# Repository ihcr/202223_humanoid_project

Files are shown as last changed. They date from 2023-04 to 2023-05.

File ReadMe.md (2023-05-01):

# 22-23 Humanoid Project Repository
This repository contains files for a humanoid robot developed in L4 project by group 93. It contains CAD designs of mechanical structure of a robot, electrical circuit design and low-level control software for its actuation system as well as test results of Unitree A1 motor tests.

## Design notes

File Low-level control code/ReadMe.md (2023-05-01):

# Introduction
This library is used for the communication between PC and multiple motor control boards via multiple converters, so that the user can control the motors by PC. This library only includes Linux version, and we offer the usage example of C++. 

# Dependencies
* [CMake](http://www.cmake.org) (version 2.8.3 or higher)
  
# Files
## /lib
Including the library files of Linux. Please modify the CMakeList manually to select the correst `.so` file.
## /include
Including the header files. ActuationSystem header file is the top-level class encapsulating the library developed for interaction with an actuation system of developed humanoid. 4 functions are needed to use it: constructor, read_actual_positions(), send_desired_positions() and update_torque().
## /src
Including the source files of example, changeID tool, code used for motor testing. The example code can control motors to run under desired command for desired time, and then stop. The main control file is motor_control.cpp which allows for testing the developed ActuationSystem class.
## /build
Build directory. The final executable files are also in this directory.

# Usage
## Setup
Go to configuration.yml and make sure that appropriate lines are commented out as per description above a list. The content of the file should reflect connected setup, i.e. number of converters and number of motors per converter.

## Build
```bash
mkdir build
cd build
cmake ..
make
```
## Run test code
```bash
cd build
sudo ./test_motor
```
## Run the main control
```bash
cd build
sudo ./motor_control
```
## Change ID
```bash
cd build
sudo ./changeID
```

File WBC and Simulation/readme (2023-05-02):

How to run demosntrations for the humanoid robot design:

Install all required libraries to run the WBC

After opening a new terminal, enter the command '. install/setup.bash'

If changing code other than yaml, urdf, or demo files, you must run 'colcon build' to implement the changes.

For Demonstration: Picking up a box off a table:
  
  at the bottom of '/src/limbsim/python/limbsim/env.py', uncomment the section labelled as being for the table demonstration and comment the other sets of objects
  
  run 'python3 src/arm_ik_wbc/demos/humanoid_demo_table.py /configs/project_humanoid_robot.yaml'

For Demonstration: Picking up a box off the floor:
  
  at the bottom of '/src/limbsim/python/limbsim/env.py', uncomment the section labelled as being for the floor demonstration and comment the other sets of objects
  
  run 'python3 src/arm_ik_wbc/demos/humanoid_demo_floor.py /configs/project_humanoid_robot.yaml'

------------------------------------------------------------------------------------------------------------------------------

The final URDF and meshes used in the demonstrations are found in /src/arm_ik_wbc/models/project_humanoid_robot
The final .yaml file used in the demonstrations is found in /src/arm_ik_wbc/configs/project_humanoid_robot.yaml

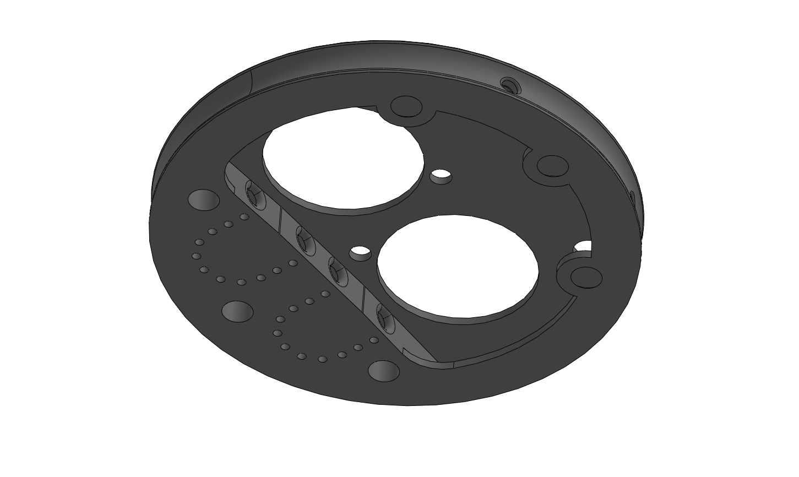
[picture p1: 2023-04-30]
CAD/Arms-Final Design/Images/Pulley-Sheave SLA.png

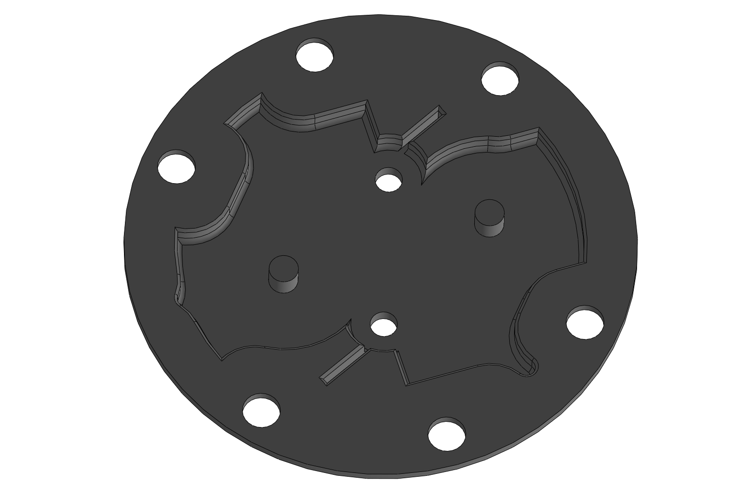
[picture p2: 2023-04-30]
CAD/Arms-Final Design/Images/Pulley-Pretensioner Bracket SLA.png

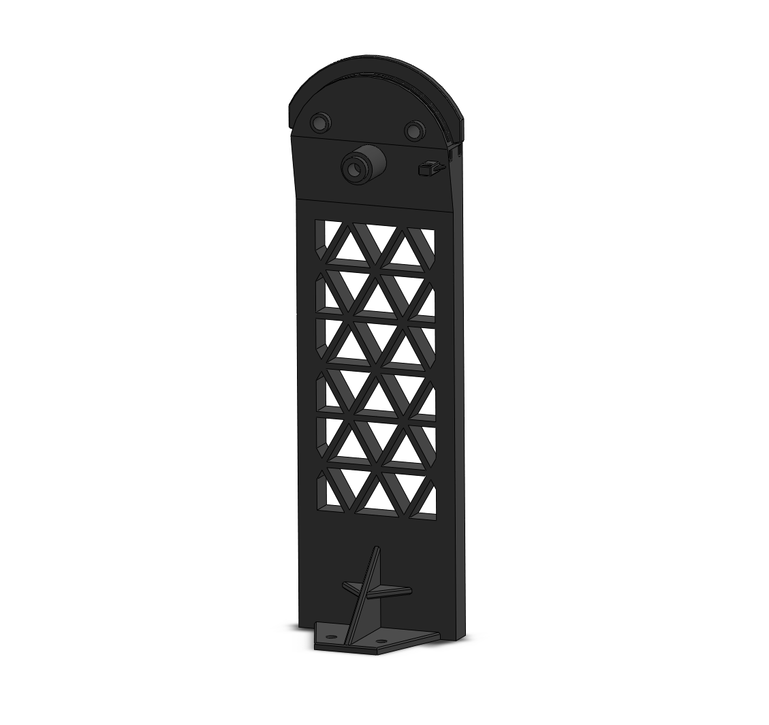
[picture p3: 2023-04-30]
CAD/Arms-Final Design/Images/Skeleton-Forearm Back.png

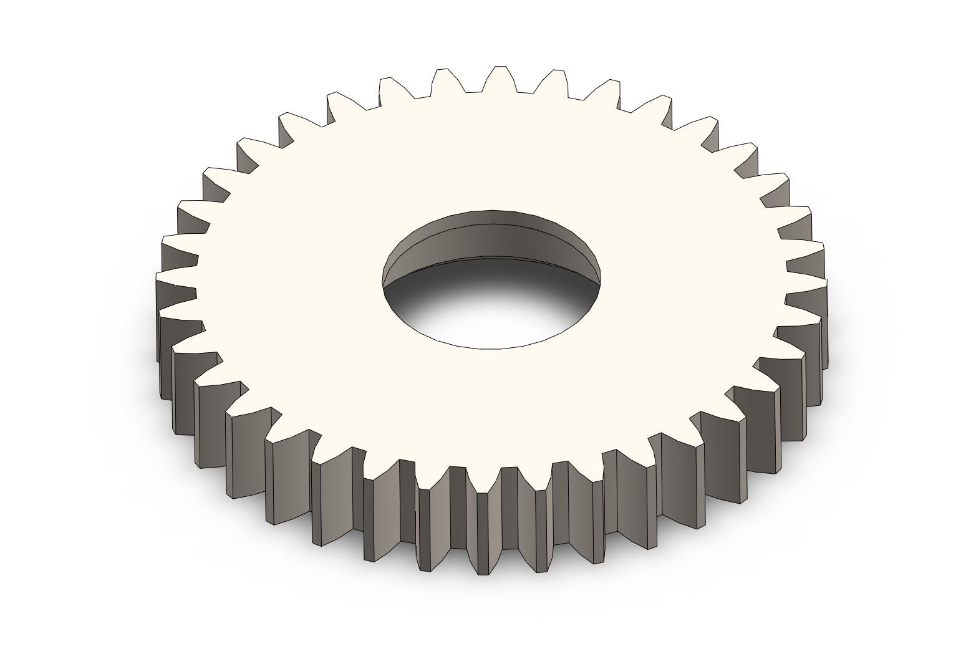
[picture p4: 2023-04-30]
CAD/Arms-Final Design/Images/Planetary Gearbox-Planet.png

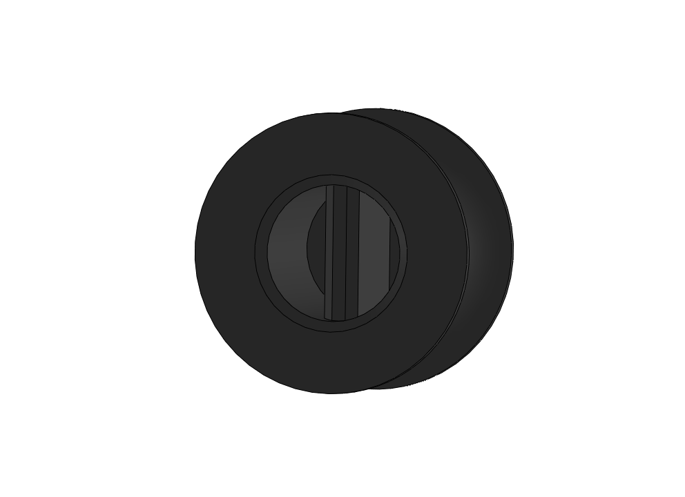
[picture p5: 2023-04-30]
CAD/Arms-Final Design/Images/Pulley-1DOF Fixed.png

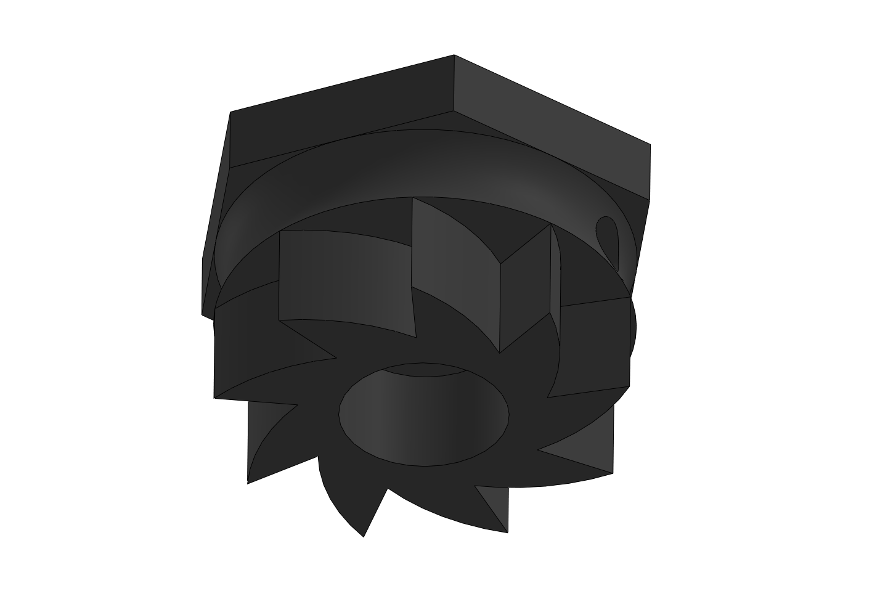
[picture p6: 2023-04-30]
CAD/Arms-Final Design/Images/Pulley-Pretensioner Ratchet SLA.png

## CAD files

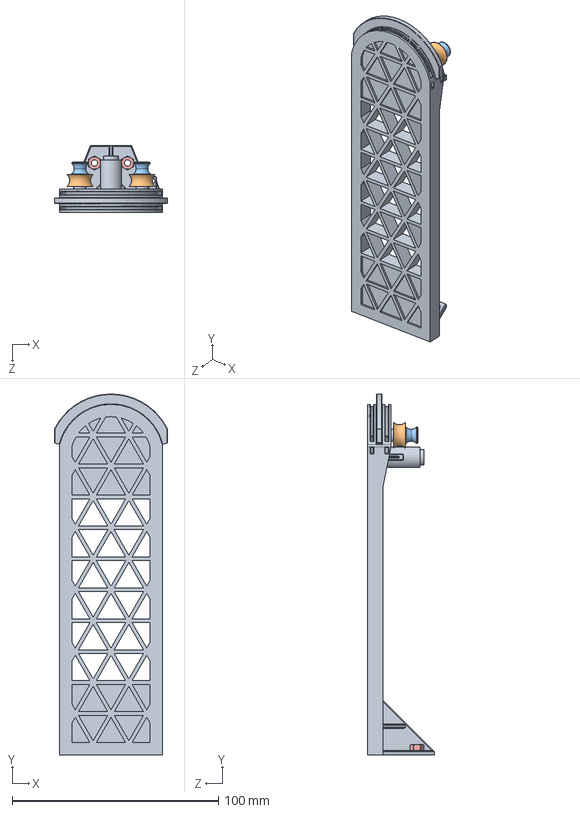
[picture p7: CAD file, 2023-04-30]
CAD/Arms-Final Design/SLDWRKS/Forearm Assembly F.SLDASM
54.8 x 175.0 x 32.5 mm
Skeleton-Forearm Front
Pulley-9mm x 2
Pulley-1DOF Fixed x 2
9mm Bearing x 2
M3 Nut x 2

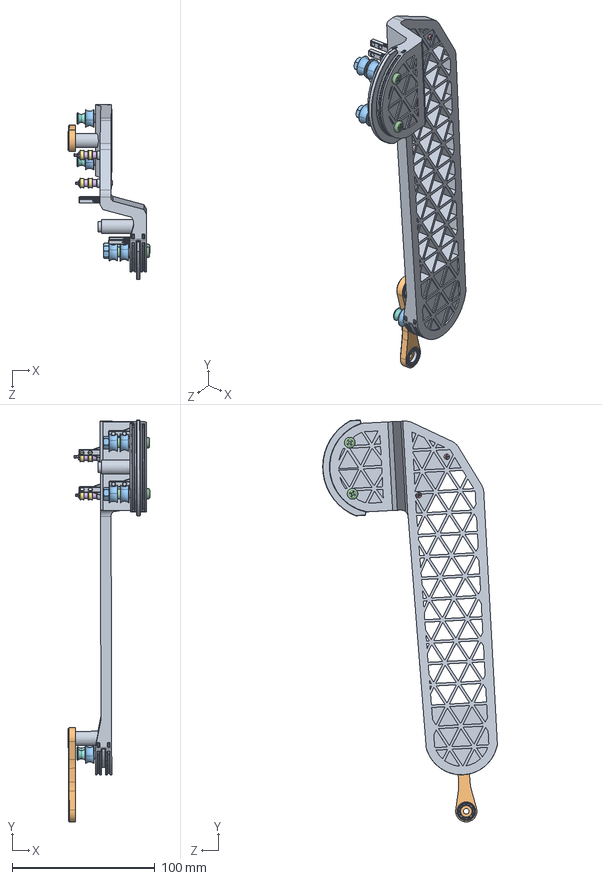
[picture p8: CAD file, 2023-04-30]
CAD/Arms-Final Design/SLDWRKS/Upper Arm Assembly F.SLDASM
57.3 x 282.0 x 122.6 mm
Skeleton-Upper Arm Front
9mm Bearing x 6
Pulley-9mm x 6
Pulley-9mm Spacer x 2
5mm Bearing x 4
Pulley-5mm Spacer x 4
Pulley-5mm ID x 4
Pulley-1DOF Fixed x 2
12mm Bearing x 2
Skeleton-Forearm Connecting Bone
M4 Nut x 2
M4x30 x 2
M2x25 x 2
M2 Nut x 2

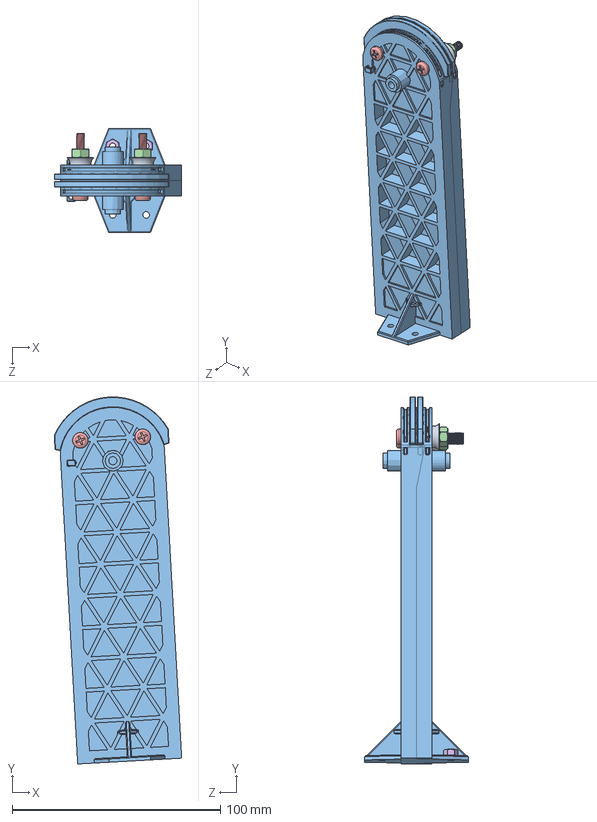
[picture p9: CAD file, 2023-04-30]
CAD/Arms-Final Design/SLDWRKS/Forearm Assembly B.SLDASM
61.2 x 176.1 x 50.0 mm
Pulley-9mm x 2
9mm Bearing x 2
Skeleton-Forearm Back
M4 Nut x 2
M4x30 x 2
M3 Nut x 2

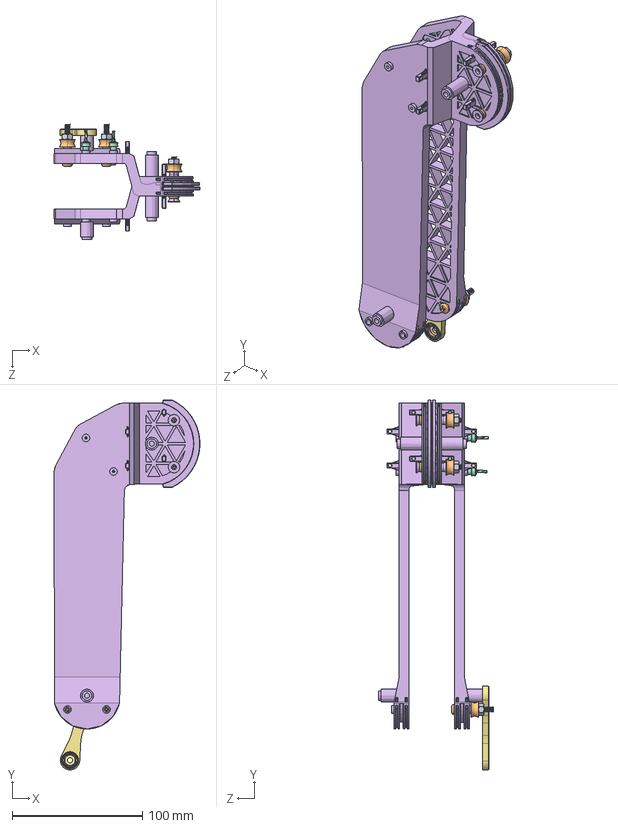
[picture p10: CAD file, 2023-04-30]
CAD/Arms-Final Design/SLDWRKS/Upper Arm Assembly B.SLDASM
111.9 x 283.9 x 88.5 mm
9mm Bearing x 4
Pulley-9mm x 4
5mm Bearing x 2
Pulley-5mm ID x 2
12mm Bearing x 2
Skeleton-Upper Arm Back
Skeleton-Forearm Connecting Bone
Pulley-5mm Spacer x 2
M4 Nut x 4
M4x30 x 4
M2 Nut x 2
M2x25 x 2

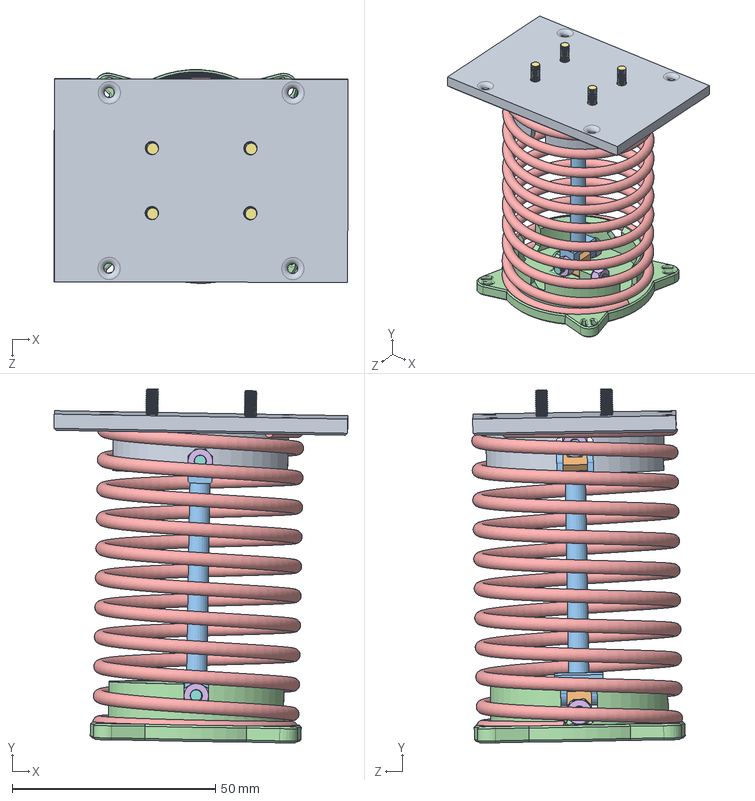
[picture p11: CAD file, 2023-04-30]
CAD/Arms-Final Design/SLDWRKS/Wrist Assembly.SLDASM
72.4 x 87.2 x 52.6 mm
Skeleton-Wrist Top
Skeleton-Wrist Universal Joint Connector x 2
Skeleton-Wrist Linkage
Skeleton-Wrist Bottom
Compression Spring
M3 Nut x 7
M3x10 x 4
M3x20 x 4

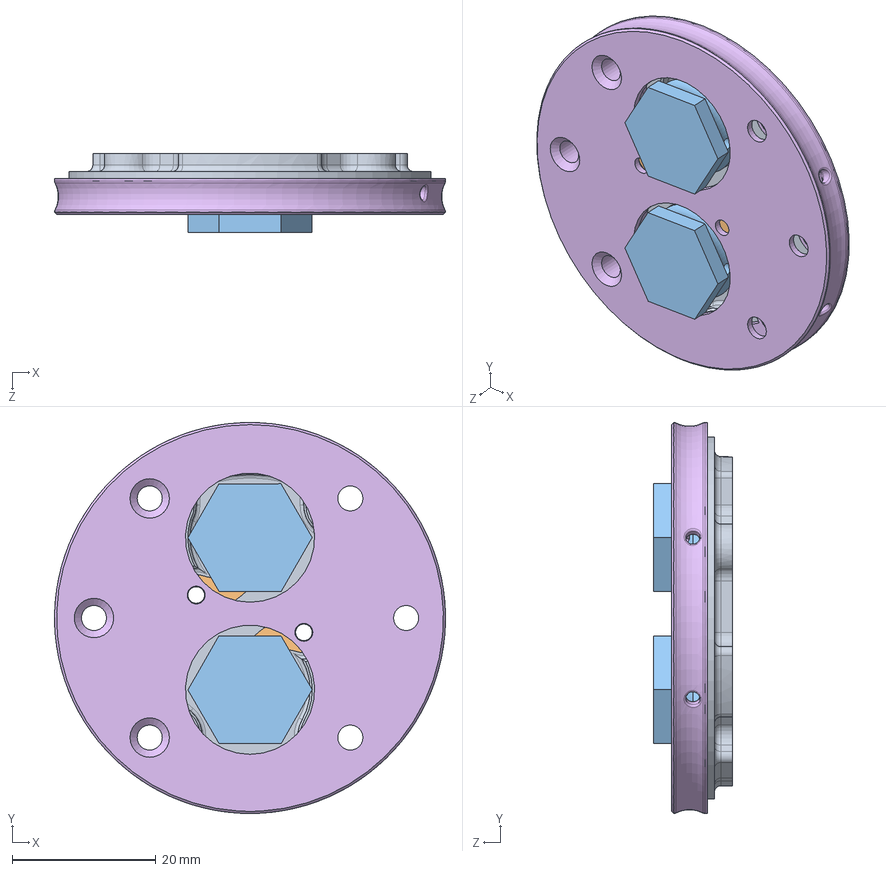
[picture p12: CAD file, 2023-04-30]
CAD/Arms-Final Design/SLDWRKS/Tensioner Assembly SLA.SLDASM
54.5 x 54.5 x 11.0 mm
Pulley-Pretensioner Bracket SLA
Pulley-Pretensioner Pawl SLA x 2
Pulley-Pretensioner Ratchet SLA x 2
6mm Bearing x 2
Torsion Spring x 2
Pulley-Sheave SLA

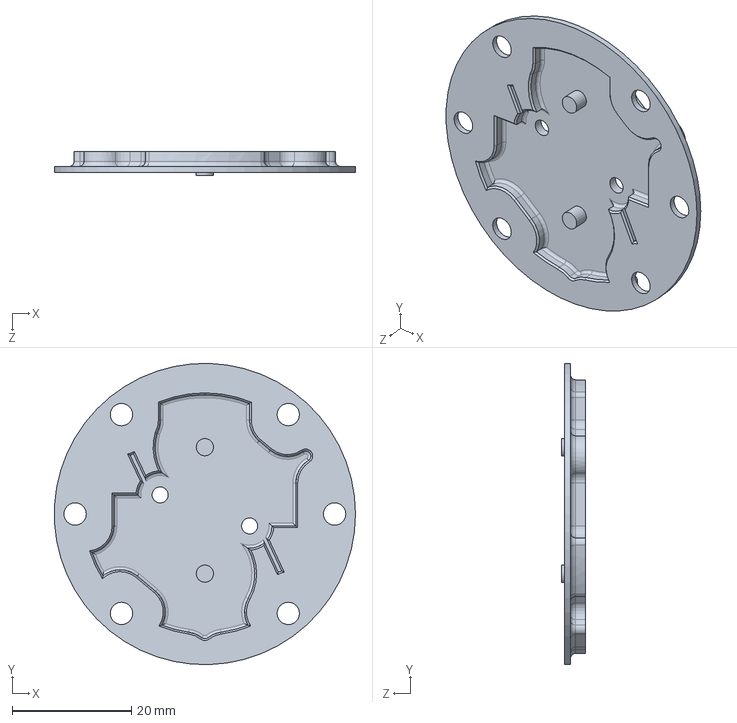
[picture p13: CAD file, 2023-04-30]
CAD/Arms-Final Design/SLDWRKS/Pulley-Pretensioner Bracket SLA.SLDPRT
50.5 x 50.5 x 4.00 mm

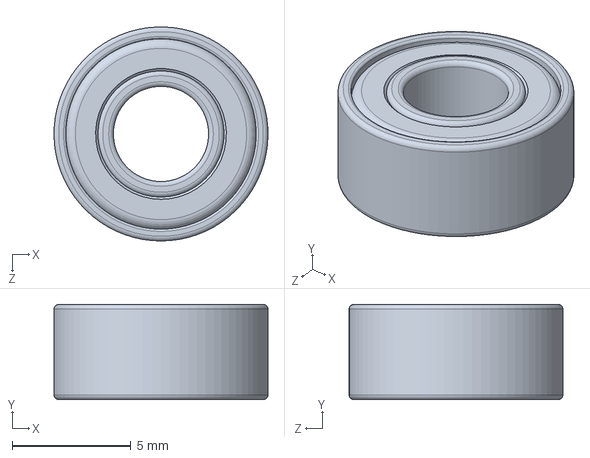
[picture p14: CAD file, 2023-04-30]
CAD/Arms-Final Design/SLDWRKS/Purchased Components/9mm Bearing.SLDPRT
9.00 x 4.00 x 9.00 mm

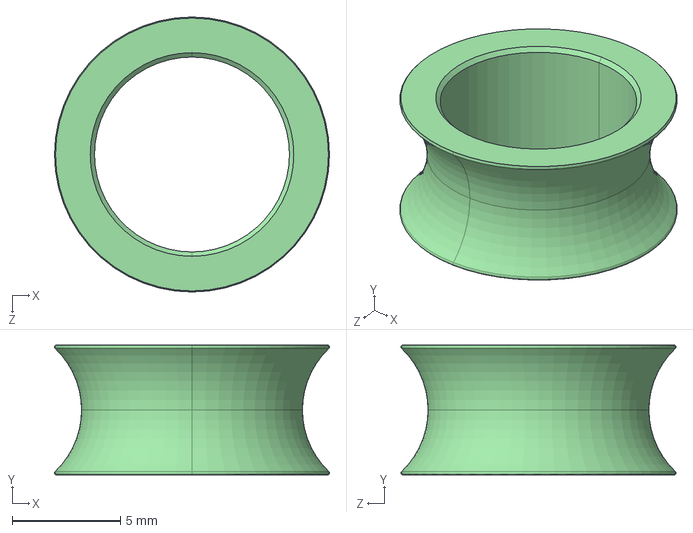
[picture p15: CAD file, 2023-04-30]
CAD/Arms-Final Design/STEP Files/Pulley-9mm.STEP
12.7 x 6.00 x 12.7 mm

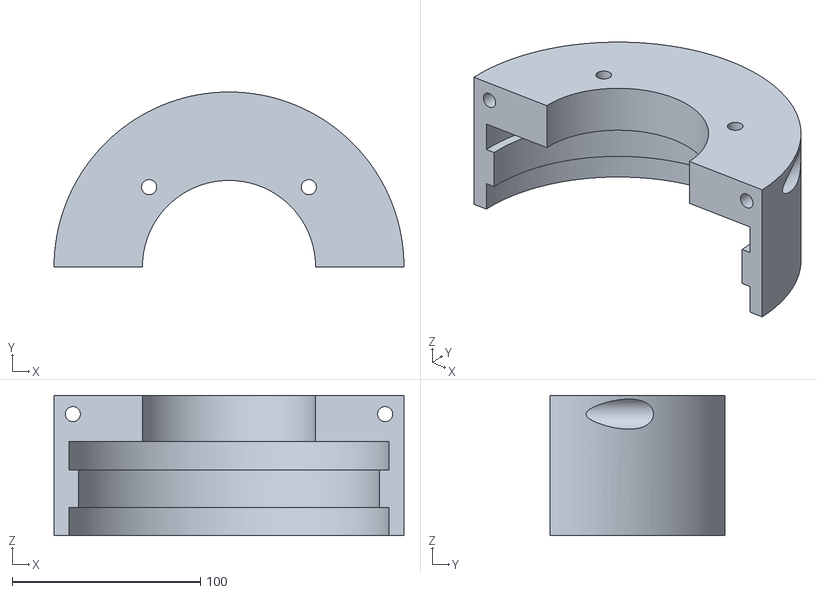
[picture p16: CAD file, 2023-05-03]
Humanoid Robot Leg Design/Humanoid_Robot_Leg_Design_Final - Hip Frame Front.stl
186.0 x 93.0 x 74.6

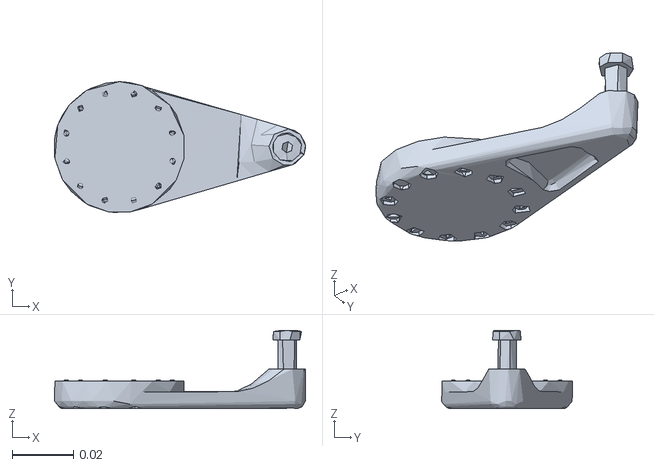
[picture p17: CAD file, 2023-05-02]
WBC and Simulation/src/arm_ik_wbc/models/cassie/meshes/right-foot-crank.stl
0.0823 x 0.0429 x 0.0257

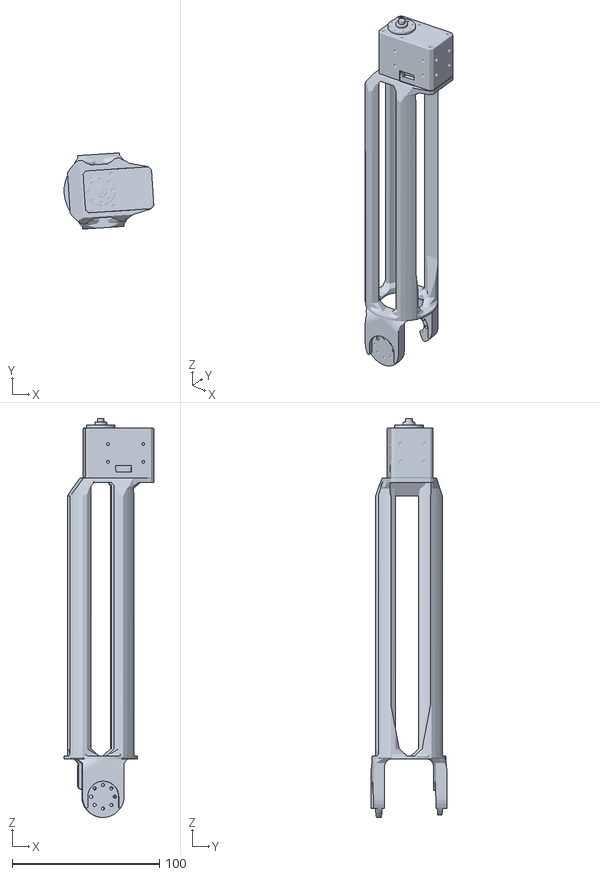
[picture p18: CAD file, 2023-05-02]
WBC and Simulation/src/arm_ik_wbc/models/cx300s/cx300s_meshes/forearm.stl
60.9 x 51.8 x 270.8

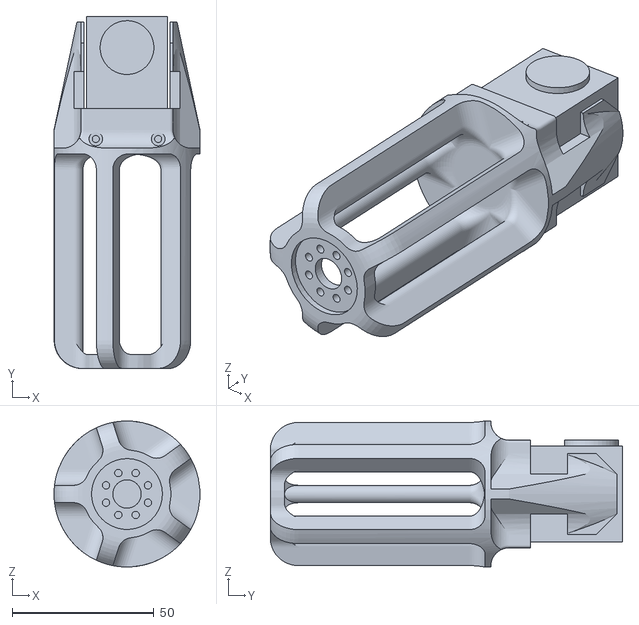
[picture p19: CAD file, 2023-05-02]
WBC and Simulation/src/arm_ik_wbc/models/dofarm/dofarm/wrist.STL
51.5 x 124.3 x 51.5

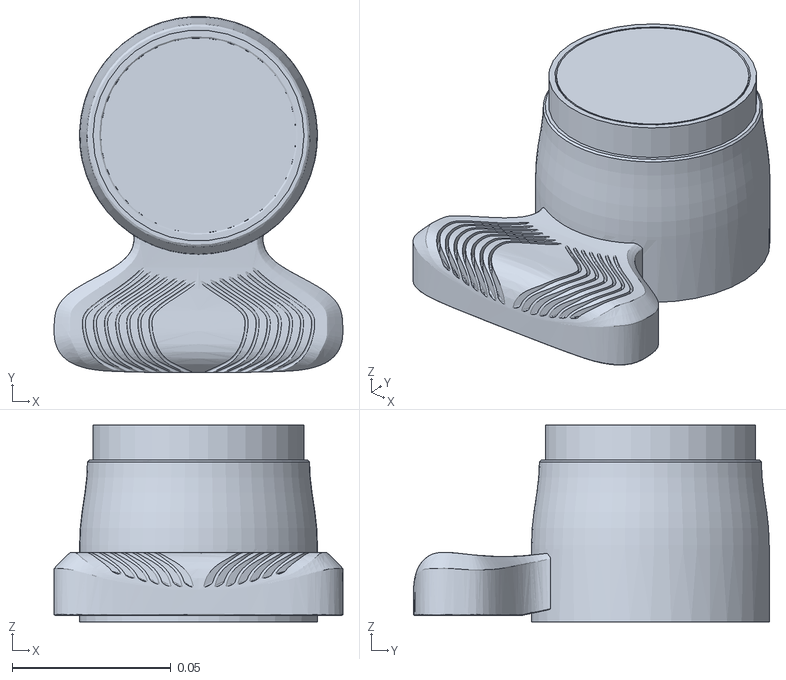
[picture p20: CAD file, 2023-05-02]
WBC and Simulation/src/arm_ik_wbc/models/kinova_7dof/meshes/bracelet_with_vision_link.STL
0.091 x 0.112 x 0.0619

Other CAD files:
WBC and Simulation/src/arm_ik_wbc/models/plane/plane.obj
WBC and Simulation/src/arm_ik_wbc/models/poppy/poppy_meshes/chest_respondable.STL
WBC and Simulation/src/arm_ik_wbc/models/project_humanoid_robot/hitboxes/right_mid_hip.STL
WBC and Simulation/src/arm_ik_wbc/models/project_humanoid_robot/meshes/left_upper_leg.STL
CAD/Arms-Final Design/SLDWRKS/Planetary Gearbox-Annulus.SLDPRT
CAD/Arms-Final Design/SLDWRKS/Planetary Gearbox-Carrier Roll.SLDPRT
CAD/Arms-Final Design/SLDWRKS/Planetary Gearbox-Carrier Yaw.SLDPRT
CAD/Arms-Final Design/SLDWRKS/Planetary Gearbox-Lid.SLDPRT
CAD/Arms-Final Design/SLDWRKS/Planetary Gearbox-Planet.SLDPRT
CAD/Arms-Final Design/SLDWRKS/Planetary Gearbox-Sun.SLDPRT
CAD/Arms-Final Design/SLDWRKS/Pulley-1DOF Fixed.SLDPRT
CAD/Arms-Final Design/SLDWRKS/Pulley-5mm ID.SLDPRT
CAD/Arms-Final Design/SLDWRKS/Pulley-5mm Spacer.SLDPRT
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

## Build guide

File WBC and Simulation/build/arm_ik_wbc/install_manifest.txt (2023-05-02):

/home/will/humanoid_ws/install/arm_ik_wbc/lib/python3.8/site-packages/arm_ik_wbc/optional/local_cartesian_constraint.py
/home/will/humanoid_ws/install/arm_ik_wbc/lib/python3.8/site-packages/arm_ik_wbc/optional/collision_constraint.py
/home/will/humanoid_ws/install/arm_ik_wbc/lib/python3.8/site-packages/arm_ik_wbc/optional/com_stability_constraint.py
/home/will/humanoid_ws/install/arm_ik_wbc/lib/python3.8/site-packages/arm_ik_wbc/optional/com_stability_task.py
/home/will/humanoid_ws/install/arm_ik_wbc/lib/python3.8/site-packages/arm_ik_wbc/com_cartesian_task.py
/home/will/humanoid_ws/install/arm_ik_wbc/lib/python3.8/site-packages/arm_ik_wbc/QP_Wrapper.py
/home/will/humanoid_ws/install/arm_ik_wbc/lib/python3.8/site-packages/arm_ik_wbc/cartesian_constraint.py
/home/will/humanoid_ws/install/arm_ik_wbc/lib/python3.8/site-packages/arm_ik_wbc/inverse_kinematics_task.py
/home/will/humanoid_ws/install/arm_ik_wbc/lib/python3.8/site-packages/arm_ik_wbc/joint_task.py
/home/will/humanoid_ws/install/arm_ik_wbc/lib/python3.8/site-packages/arm_ik_wbc/trajectory_planner.py
/home/will/humanoid_ws/install/arm_ik_wbc/lib/python3.8/site-packages/arm_ik_wbc/ik_wbc.py

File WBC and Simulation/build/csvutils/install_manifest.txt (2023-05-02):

/home/will/humanoid_ws/install/csvutils/lib/libcsvutils.so
/home/will/humanoid_ws/install/csvutils/include/csvutils/csv_writer.hpp
/home/will/humanoid_ws/install/csvutils/share/csvutils/cmake/csvutilsConfig.cmake
/home/will/humanoid_ws/install/csvutils/share/csvutils/cmake/csvutilsConfigVersion.cmake
/home/will/humanoid_ws/install/csvutils/share/csvutils/cmake/csvutilsTargets.cmake
/home/will/humanoid_ws/install/csvutils/share/csvutils/cmake/csvutilsTargets-noconfig.cmake

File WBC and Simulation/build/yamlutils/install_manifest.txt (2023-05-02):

/home/will/humanoid_ws/install/yamlutils/include/yamlutils/yaml_cpp_fwd.hpp
/home/will/humanoid_ws/install/yamlutils/include/yamlutils/yaml_eigen.hpp
/home/will/humanoid_ws/install/yamlutils/include/yamlutils/yaml_tools.hpp
/home/will/humanoid_ws/install/yamlutils/share/yamlutils/cmake/yamlutilsConfig.cmake
/home/will/humanoid_ws/install/yamlutils/share/yamlutils/cmake/yamlutilsConfigVersion.cmake
/home/will/humanoid_ws/install/yamlutils/share/yamlutils/cmake/yamlutilsTargets.cmake

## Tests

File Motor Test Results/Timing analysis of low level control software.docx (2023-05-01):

# Timing analysis of the motor control code

## Code setup

Execution times of functions below were obtained using the following code template:

#include <chrono>

auto start = std::chrono::high_resolution_clock::now();

<function to be checked for execution time>;

auto end = std::chrono::high_resolution_clock::now();

auto duration = std::chrono::duration_cast<std::chrono::microseconds>(end - start);

std::cout << "Execution time of function: " << duration.count() << " microseconds" << std::endl;

## Investigated code

//function to loop through all MotorGroup objects to calculate new value of torque

void ActuationSystem::update_torque(){

std::vector<std::thread> threads; //vector to store threads

//loop to put torque update function threads into the vector

for (int i = 0; i < _number_of_converters; i++) {

threads.emplace_back(std::thread(&MotorGroup::update_torque, _motor_groups[i]));

}

//loop to merge the threads

for (auto& t : threads) {

t.join();

}

}

update_torque() function in ActuationSystem class iterating through all connected converters.

void MotorGroup::update_torque(){

//a loop to iterate through all the motors

//std::cout << "Entered MotorGroup::update_torque()"<< std::endl;

for(int i = 0; i < _number_of_motors; i++){

//auto start = std::chrono::high_resolution_clock::now();

sendRecv(&_motors[i].motor_run, &_motors[i].motor_r); //send an initial message to the motor and receive data from it

extract_data(&_motors[i].motor_r); //extract data from the received message

//auto end = std::chrono::high_resolution_clock::now();

//auto duration = std::chrono::duration_cast<std::chrono::microseconds>(end - start);

//std::cout << "Execution time of sendRecv() and extract_data(): " << duration.count() << " microseconds" << std::endl;

_motors[i].new_torque(); //update motor's torque

}

}

update_torque() function in MotorGroup class iterating through all connected to a converter motors.

## Test setups

Setup 1:

- USB hub connected
- 2 converters connected
- 1 motor on converter 0 and 3 motors on converter 1
- Update_torque() function in ActuationSystem has no thread function paralellising the for loop

Result:

Function | Measured execution time [μs]
ActuationSystem::Read_actual_positions() | 1
ActuationSystem:: Send_desired_positions | 8
ActuationSystem:: Update_torque | 4000

Setup 2:

- USB hub connected
- 2 converters connected
- 1 motor on converter 0 and 3 motors on converter 1
- Update_torque() function in ActuationSystem has thread function paralellising the for loop

Result:

Function | Measured execution time [μs]
ActuationSystem::Read_actual_positions() | 1
ActuationSystem:: Send_desired_positions | 8
ActuationSystem:: Update_torque | 3000

Setup 3:

- No USB hub connected
- 1 converter
- 3 motors on converter 0
- Update_torque() function in ActuationSystem has thread function paralellising the for loop

Result:

Function | Measured execution time [μs]
ActuationSystem::Read_actual_positions() | 1
ActuationSystem:: Send_desired_positions | 7
ActuationSystem:: Update_torque | 3000

Setup 4:

- No USB hub connected
- 1 converter
- 3 motors on converter 0
- Update_torque in ActuationSystem has no thread function paralellising the for loop

Result:

Function | Measured execution time [μs]
ActuationSystem::Read_actual_positions() | 1
ActuationSystem:: Send_desired_positions | 8
ActuationSystem:: Update_torque | 3000

Setup 5:

- No USB hub connected
- 1 converter
- 3 motors on converter 0
- Update_torque in ActuationSystem has no thread function paralellising the for loop
- Added one time measurement directly for both sendRecv and extract_data functions in MotorGroup::update_torque().

Result:

Function | Measured execution time [μs]
ActuationSystem::Read_actual_positions() | 1
ActuationSystem:: Send_desired_positions | 7
ActuationSystem:: Update_torque | 3000
SerialPort::sendRecv() + SerialPort::extract_data() | 1000

Setup 6:

- No USB hub connected
- 1 converter
- 3 motors on converter 0
- Update_torque() in ActuationSystem has thread function paralellising the for loop
- sendRecv and extract_data functions are parallelised in MotorGroup

Result:

Entered the second loop

******************

[WARNING] SerialPort::recv, unblock version, wait time out

[WARNING] motor id=0 does not reply

[WARNING] Receive data CRC error

[WARNING] SerialPort::recv, unblock version, wait time out

[WARNING] motor id=1 does not reply

[WARNING] Receive data CRC error

[WARNING] SerialPort::recv, unblock version, wait time out

[WARNING] motor id=2 does not reply

[WARNING] Receive data CRC error

Execution time of update_torque(): 21956 microseconds. Max f: 45.5456

Terminal output

## Conclusion

SerialPort:: sendRecv() and SerialPort:: extract_data() functions are a bottleneck for a quick operation of the software as they take 1 ms every time they are called, which for 3 motors per converter amounts to total execution time of 3 ms for ActuationSystem::update_torque(). This limits the program to max frequency at which it can be run of 330 Hz. The required frequency is 500 Hz.

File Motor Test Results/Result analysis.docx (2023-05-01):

# Testing of Unitree A1 motor

Unitree A1 motor’s encoder, velocity and torque properties were tested to check whether the motor meets requirements of this project’s humanoid robot.

To ensure appropriate health and safety standard velocity, torque and current tests were conducted in a cage inside which nobody was allowed when the motor was connected to a source of power. Additionally, a safety button was connected in series between power source and the motor.

## Encoder testing

To control movement of humanoid limbs a precise position of a limb is needed. This information can be provided by Unitree A1 motor’s built-in encoder but to ensure that it can provide readings of sufficient precision it must have been tested.

### Setup

The accuracy of the encoder was tested by placing the motor with attached to the rotor pointer in a centre of a printed protractor as presented in Figure 1.

The motor was set to no torque mode which allowed for free rotation of the pointer by hand. Additionally, the actual output of the encoder was divided by 9.1 due to the internal gear ratio of the motor, so that the recorded values were consistent with protractor’s indication.

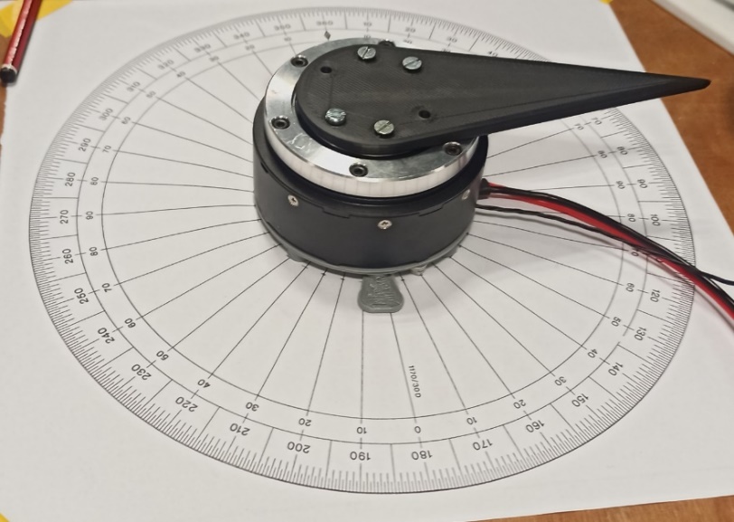
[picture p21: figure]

Figure 1 Encoder testing setup

### Steps

Initially, rotor’s position was aligned with the protractor so that both indicated 90°. Then the rotor was moved ten times by 180° to verify the accuracy of repeated movement which was followed by 11 full revolutions and two more 180° rotations to check whether the error is affected by the magnitude of a move. The remaining readings were verifying whether the error changes for small rotations. The recorded values are presented in Figure 2.

Reading number | Done motion [°] | Encoder reading [°] | Protractor [°] | Error [°]
1 | Initial position | 90 | 90 | 0
2 | 180 | 270.068 | 270 | 0.068
3 | 180 | 449.097 | 450 | 0.903
4 | 180 | 630.442 | 630 | 0.442
5 | 180 | 808.899 | 810 | 1.101
6 | 180 | 990.307 | 990 | 0.307
7 | 180 | 1168.976 | 1170 | 1.024
8 | 180 | 1350.956 | 1350 | 0.956
9 | 180 | 1528.826 | 1530 | 1.174
10 | 180 | 1710.626 | 1710 | 0.626
11 | 180 | 1888.916 | 1890 | 1.084
12 | 3960 | 5848.556 | 5850 | 1.444
13 | 180 | 6030.426 | 6030 | 0.426
14 | 180 | 6208.576 | 6210 | 1.424
15 | 90 | 6299.016 | 6300 | 0.984
16 | 30 | 6330.036 | 6330 | 0.036
17 | 60 | 6390.196 | 6390 | 0.196
18 | 270 | 6659.426 | 6660 | 0.574

Figure 2 Recorded outputs of encoder and protractor readings.

### Discussion of encoder test results

Errors between protractor indications and encoder readings are mostly affected by the difficulty of precise positioning of the rotor’s pointer on the protractor because of the torque required to move the rotor that was slightly dropping once the rotor was moving which caused overshooting. Additionally, rotor’s position could have been measured with precision of up to 1° as that was the resolution of the protractor.

The average value of the errors amounted to 0.75°, with the maximum error of a single measurement equal to 1.4°. Such result of the test lies within a reasonable tolerance considering sources of error that the test was burdened with as described above. This proves that motor’s encoder is suitable for indicating positions of humanoid’s limbs with sufficient precision.

## Velocity testing

Humanoid robot’s limbs must move with enough speed to perform swift movements. To make sure that Unitree A1 motor can reach maximum desired velocity at a torque mimicking motion of a limb a velocity test was performed. Therefore, flexion of the designed arm at the speed of 1 rpm generating 0.8 Nm was taken as a point of reference.

### Test setup

Due to limited components suitable for imitating of the arm, test torque was increased to 1.12 Nm. It was exerted by an attached to the rotor lever when in parallel to the ground position (Figure 3).

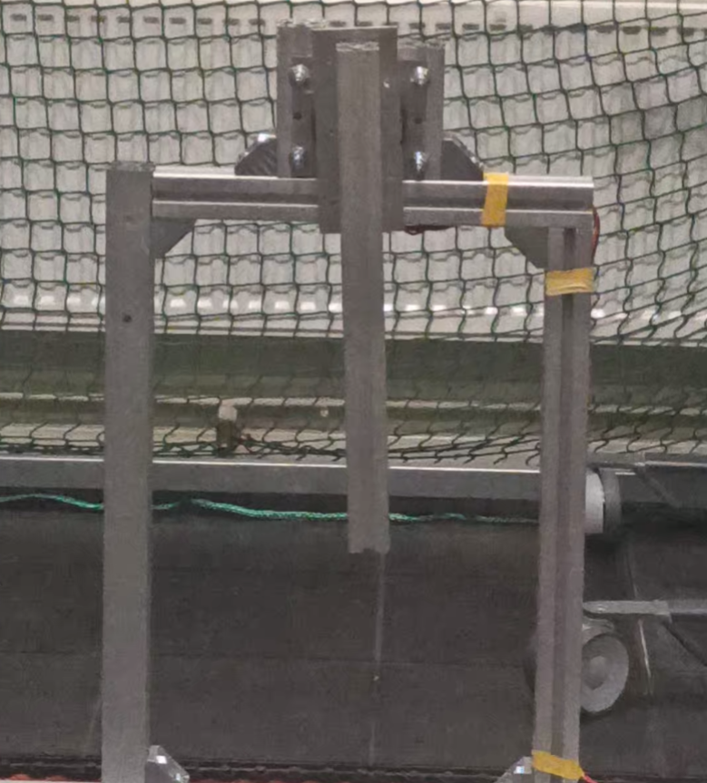
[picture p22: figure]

Figure 3 Velocity test setup

### Steps

The motor was gradually accelerated to the maximum desired velocity of 2π rad/s which was then maintained for a few seconds. Motor’s velocity was calculated from a video of the test by multiplying number of frames per rotation by the inverse of frame rate of the camera equal to 60 fps (Figure 4).

Start time of a rotation [s] | End time a rotation [s] | Time difference [s] | Average velocity of a rotation [rad/s] | Error between desired and measured velocity [rad/s]
5.832 | 6.865 | 1.033 | 6.082 | 0.200
6.865 | 7.898 | 1.033 | 6.082 | 0.200
7.898 | 8.931 | 1.033 | 6.082 | 0.200
8.931 | 9.964 | 1.033 | 6.082 | 0.200

Figure 4 Motor's velocity measured using a camera

### Discussion of velocity test results

The test was burdened with measurement inaccuracies such as the frame rate of the camera which limits the precision of the measurement to 0.017s as well as difficulty in precise identification of the moment when a full rotation was completed. These factors contributed towards obtaining the difference between desired and measured speed.

Values obtained from the video of the test (Figure 4) show that the Unitree A1 motor is capable of stable running close to the desired speed at the applied torque. The error is consistent throughout the duration of the test and equal to 3% which is a satisfactory result. The reason for the velocity difference could be a varying torque acting on the motor due to the constantly changing angle between the centre of the mass of the lever and gravitational acceleration.

## Torque testing

One of the key information in the design of an actuation mechanism of a humanoid robot is the amount of available torque. Therefore, a test evaluating the maximum torque of the Unitree A1 motor was designed and performed.

### Test setup

A lever was attached to the rotor, so that an additional mass generating required torque could have been hanged on it. To ensure that the lever was in a parallel to the ground position in the beginning of the test, which maximised generated torque and simplified its calculation, a beam cut to an appropriate length was used as a support which was removed once the motor was powered up (Figure 5). A proportional controller was used for the control of the motor during the test.

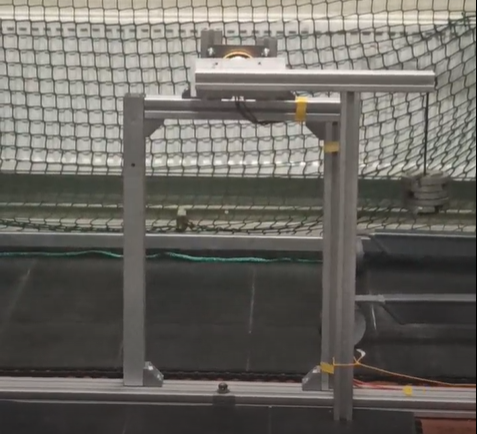
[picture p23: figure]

Figure 5 Torque test setup

### Steps

To minimise risk of breaking the motor the test had multiple iterations between which proportional controller gain was increased until the motor was not letting the lever to rotate downwards. Once that was achieved the mass at the end of the lever was increased and controller’s gain was iteratively increased again. This process continued until the maximum torque of the motor was achieved.

The torque was calculated by measuring length of the lever and its mass as well as by weighting the additional mass attached to it. These values allowed for estimation of the torque experienced by the rotor considering lever’s deviation from the horizontal position due to the acting torque. The calculated value was then compared to the torque reading from the motor.

The maximum torque was calculated considering inertia of the setup and deviation angle from horizontal position once the motor stabilised and amounting to 0.65 rad (Figure 7). The calculated torque equals to 32.5 Nm. Motor’s torque sensor output indicated 33.5 Nm (Figure 6).

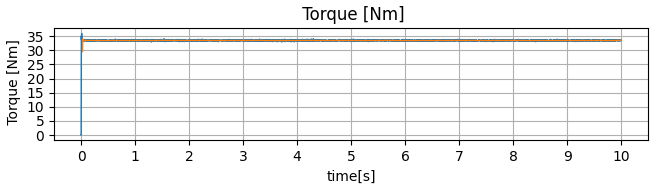
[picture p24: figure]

Figure 6 Output of motor's torque sensor at the maximum torque.

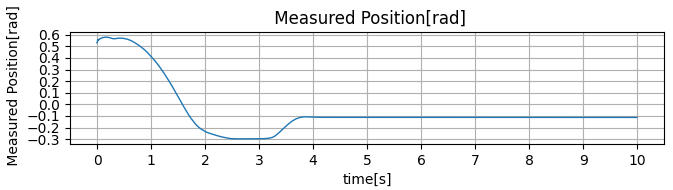
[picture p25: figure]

Figure 7 Output of motor's encoder at the maximum torque test

### Discussion of torque test results

The test was burdened with measurement inaccuracies such as 0.01 kg resolution of the scale used for weighting the lever and additional weights, obtained above motor’s encoder average reading precision of 0.75° used for determining the deviation from the horizontal position as well as difficulty in precise measuring of the distance between the weight’s point of attachment and centre of rotation. Moreover, assumption that initial position of the lever is horizontal in every iteration introduced additional inaccuracy.

The maximum torque of the motor obtained in the test equals to 32.5 Nm and differs from the datasheet value of 33.5 Nm by 1 Nm. This equals to 3% discrepancy, which places the result within a satisfactory margin of error.

## Maximum current testing

A Permanent Magnet Synchronous Motor (PMSM) such as Unitree A1 motor is characterised by a linear correlation between torque and current hence to design a wiring loom of appropriate current rating current drawn at maximum torque must be determined.

### Test setup and steps

Setup, test steps, measurements and calculations for the drawn current testing are identical as for the torque testing described above with addition of recording current drawn by the motor with a clamp meter.

Figure 8 Torque vs current characteristic of the motor.

### Discussion of torque test results

Apart from the source of error discussed in torque testing section above, this test was additionally burdened with notable imprecision of the current reading. It had a lot of noise and positive offset of approximately 0.25 A when compared with the reading from the power supply for currents below 4 A. However, the test itself was supposed to provide only a point of reference of the maximum current value for the current rating of a wiring loom for the motors. Therefore, such large inaccuracies of the test are acceptable.

Obtained curve of current vs torque characteristics (Figure 8) resembles a straight line as it is expected for a permanent magnet synchronous motor such as Unitree A1 motor (https://ieeexplore.ieee.org/stamp/stamp.jsp?tp=&arnumber=25541 + power electronics book). The maximum current that occurs at maximum torque is estimated to be 20 A. Therefore, the wiring loom should be designed to operate above this value.

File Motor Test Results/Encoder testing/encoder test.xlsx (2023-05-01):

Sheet: Sheet1
Reading number | Done motion[deg] | Encoder [deg] | Protractor [deg] | error [deg] | error before gears[deg] | initial offset | 81.595 |  | encoder diff
1 | Initial position | 8.405 | 90 | 0 | 0
2 | 180 | 169.955 | 270 | 18.45 | 2.027472527 |  |  | 180 | 161.55 | 18.45
3 | 180 | 351.443 | 450 | 16.962 | 1.863956044 |  |  | 180 | 181.488 | -1.488
4 | 180 | 530.274 | 630 | 18.131 | 1.992417582 |  |  | 180 | 178.831 | 1.169
5 | 180 | 711.43 | 810 | 16.975 | 1.865384615 |  |  | 180 | 181.156 | -1.156
6 | 180 | 889.755 | 990 | 18.65 | 2.049450549 |  |  | 180 | 178.325 | 1.675
7 | 180 | 1071.87 | 1170 | 16.535 | 1.817032967 |  |  | 180 | 182.115 | -2.115
8 | 180 | 1249.58 | 1350 | 18.825 | 2.068681319 |  |  | 180 | 177.71 | 2.29
9 | 180 | 1431.8 | 1530 | 16.605 | 1.824725275 |  |  | 180 | 182.22 | -2.22
10 | 180 | 1609.88 | 1710 | 18.525 | 2.035714286 |  |  | 180 | 178.08 | 1.92
11 | 180 | 1791.63 | 1890 | 16.775 | 1.843406593 |  |  | 180 | 181.75 | -1.75
12 | 3960 | 5751.44 | 5850 | 16.965 | 1.864285714 |  |  | 3960 | 3959.81 | 0.19
13 | 180 | 5929.8 | 6030 | 18.605 | 2.044505495 |  |  | 180 | 178.36 | 1.64
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

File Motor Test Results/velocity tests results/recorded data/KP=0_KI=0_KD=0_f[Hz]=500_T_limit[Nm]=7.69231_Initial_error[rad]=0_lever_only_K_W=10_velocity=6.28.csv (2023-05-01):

KP=0 KI=0 KD=0 f[Hz]=500 T_limit[Nm]=7.69231 Initial error[rad]=0 lever only | 0 | 0 | 0 | 0 | 0 | 0 | 0 | 0 | 0 | 0
time[s] | Position Error[rad] | Target Position[rad] | Measured Position[rad] | Integral | Derivative | PID Output[Nm] | Motor Temperature[°C] | Acceleration [rad/s^2] | Velocity [rad/s] | Torque [Nm]
0 | 0 | 0.340932 | 0.340932 | 0 | 0 | 0 | 23 | -7.58242 | -0.0206044 | 0.106641
0.002 | 0 | 0.340932 | 0.340932 | 0 | 0 | 0 | 23 | 1.86813 | 0 | 0
0.004 | 0 | 0.340932 | 0.340932 | 0 | 0 | 0 | 23 | 0.659341 | 0.00600962 | 0.355469
0.006 | -8.4281e-05 | 0.340932 | 0.341017 | -1.68562e-07 | -0.0421405 | -0 | 23 | 14.7253 | 0.195742 | -0.0710938
0.008 | -0.000126421 | 0.340932 | 0.341059 | -4.21405e-07 | -0.0210702 | -0 | 23 | 8.35165 | 0.105598 | 0.248828
0.01 | -0.000126421 | 0.340932 | 0.341059 | -6.74248e-07 | 0 | 0 | 23 | -11.978 | 0.00429258 | 0.56875
0.012 | -0.000210702 | 0.340932 | 0.341143 | -1.09565e-06 | -0.0421405 | -0 | 23 | -0.879121 | 0.175996 | 0.319922
0.014 | -0.000210702 | 0.340932 | 0.341143 | -1.51706e-06 | 0 | 0 | 23 | 3.73626 | 0.00429258 | 0.462109
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

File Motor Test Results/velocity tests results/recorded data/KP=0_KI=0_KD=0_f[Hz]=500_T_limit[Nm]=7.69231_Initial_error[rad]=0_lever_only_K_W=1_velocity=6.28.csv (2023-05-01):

KP=0 KI=0 KD=0 f[Hz]=500 T_limit[Nm]=7.69231 Initial error[rad]=0 lever only | 0 | 0 | 0 | 0 | 0 | 0 | 0 | 0 | 0 | 0
time[s] | Position Error[rad] | Target Position[rad] | Measured Position[rad] | Integral | Derivative | PID Output[Nm] | Motor Temperature[°C] | Acceleration [rad/s^2] | Velocity [rad/s] | Torque [Nm]
0 | 0 | 38.2542 | 38.2542 | 0 | 0 | 0 | 23 | 0 | 0 | 0.0355469
0.002 | 0 | 38.2542 | 38.2542 | 0 | 0 | 0 | 23 | 0 | 0 | 0.284375
0.004 | 0 | 38.2542 | 38.2542 | 0 | 0 | 0 | 23 | -1.64835 | 0.0154533 | 0.142188
0.006 | 0 | 38.2542 | 38.2542 | 0 | 0 | 0 | 23 | 5.38462 | 0.00171703 | 0.0710938
0.008 | 0 | 38.2542 | 38.2542 | 0 | 0 | 0 | 23 | -3.07692 | 0.0377747 | 0.248828
0.01 | 0 | 38.2542 | 38.2542 | 0 | 0 | 0 | 23 | -7.36264 | 0.00944368 | 0.106641
0.012 | 4.19617e-05 | 38.2542 | 38.2542 | 8.39233e-08 | 0.0209808 | 0 | 23 | -0.43956 | -0.121909 | 0.142188
0.014 | 4.19617e-05 | 38.2542 | 38.2542 | 1.67847e-07 | 0 | 0 | 23 | 0 | -0.166552 | 0.0710938
0.016 | 0 | 38.2542 | 38.2542 | 1.67847e-07 | -0.0209808 | 0 | 23 | 7.14286 | 0.00257555 | 0
0.018 | 4.19617e-05 | 38.2542 | 38.2542 | 2.5177e-07 | 0.0209808 | 0 | 23 | -4.06593 | -0.166552 | 0.0355469
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

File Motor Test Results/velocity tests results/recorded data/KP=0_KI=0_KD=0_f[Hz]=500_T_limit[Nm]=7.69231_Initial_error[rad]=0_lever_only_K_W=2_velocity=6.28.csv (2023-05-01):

KP=0 KI=0 KD=0 f[Hz]=500 T_limit[Nm]=7.69231 Initial error[rad]=0 lever only | 0 | 0 | 0 | 0 | 0 | 0 | 0 | 0 | 0 | 0
time[s] | Position Error[rad] | Target Position[rad] | Measured Position[rad] | Integral | Derivative | PID Output[Nm] | Motor Temperature[°C] | Acceleration [rad/s^2] | Velocity [rad/s] | Torque [Nm]
0 | 0 | 0.61785 | 0.61785 | 0 | 0 | 0 | 19 | -5.49451 | -0.000858516 | -0.0355469
0.002 | 0 | 0.61785 | 0.61785 | 0 | 0 | 0 | 20 | -7.14286 | 0.0317651 | -0.0355469
0.004 | 0 | 0.61785 | 0.61785 | 0 | 0 | 0 | 20 | 4.61538 | 0 | 0.0710938
0.006 | 0 | 0.61785 | 0.61785 | 0 | 0 | 0 | 20 | 0.659341 | 0 | 0.0710938
0.008 | 0 | 0.61785 | 0.61785 | 0 | 0 | 0 | 20 | 0 | 0 | 0.0710938
0.01 | 0 | 0.61785 | 0.61785 | 0 | 0 | 0 | 20 | 0 | 0 | 0.142188
0.012 | -4.22001e-05 | 0.61785 | 0.617892 | -8.44002e-08 | -0.0211 | -0 | 20 | 9.67033 | 0.100446 | 0.213281
0.014 | -4.22001e-05 | 0.61785 | 0.617892 | -1.688e-07 | 0 | 0 | 20 | -11.4286 | 0.129636 | 0.142188
0.016 | 0 | 0.61785 | 0.61785 | -1.688e-07 | 0.0211 | 0 | 20 | -7.36264 | -0.0386332 | 0.177734
0.018 | -4.22001e-05 | 0.61785 | 0.617892 | -2.53201e-07 | -0.0211 | -0 | 20 | 8.9011 | 0.0635302 | 0.106641
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

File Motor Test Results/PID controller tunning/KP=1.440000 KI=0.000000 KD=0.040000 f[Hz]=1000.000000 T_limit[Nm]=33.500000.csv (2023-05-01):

iteration | torque 0 [Nm] | actual position 0 [rad] | desired position 0 [rad]
0 | 0.00174646 | 0.058578 | 0.0586201
1 | -0.00168577 | 0.0586201 | 0.0586201
2 | 0 | 0.0586201 | 0.0586201
3 | 0 | 0.0586201 | 0.0586201
4 | 0 | 0.0586201 | 0.0586201
5 | 0 | 0.0586201 | 0.0586201
6 | 0 | 0.0586201 | 0.0586201
7 | 0 | 0.0586201 | 0.0586201
8 | 0 | 0.0586201 | 0.0586201
9 | 0 | 0.0586201 | 0.0586201
10 | 0 | 0.0586201 | 0.0586201
11 | 0 | 0.0586201 | 0.0586201
12 | 0 | 0.0586201 | 0.0586201
13 | 0 | 0.0586201 | 0.0586201
14 | 0 | 0.0586201 | 0.0586201
15 | 0 | 0.0586201 | 0.0586201
16 | 0 | 0.0586201 | 0.0586201
17 | 0 | 0.0586201 | 0.0586201
18 | 0 | 0.0586201 | 0.0586201
19 | 0 | 0.0586201 | 0.0586201
20 | 0 | 0.0586201 | 0.0586201
21 | 0 | 0.0586201 | 0.0586201
22 | -0.00174646 | 0.0586623 | 0.0586201
23 | 0.00168577 | 0.0586201 | 0.0586201
24 | -0.00174646 | 0.0586623 | 0.0586201
25 | 0.00168577 | 0.0586201 | 0.0586201
26 | 0 | 0.0586201 | 0.0586201
27 | 0 | 0.0586201 | 0.0586201
28 | 0 | 0.0586201 | 0.0586201
29 | 0 | 0.0586201 | 0.0586201
30 | 0 | 0.0586201 | 0.0586201
31 | 0.00174646 | 0.058578 | 0.0586201
32 | -0.00168577 | 0.0586201 | 0.0586201
33 | 0 | 0.0586201 | 0.0586201
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

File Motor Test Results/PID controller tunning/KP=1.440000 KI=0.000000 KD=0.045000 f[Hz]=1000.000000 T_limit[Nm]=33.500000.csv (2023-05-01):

iteration | torque 0 [Nm] | actual position 0 [rad] | desired position 0 [rad]
0 | 0.00391418 | -0.0102406 | -0.0101563
1 | 0.00012137 | -0.0102406 | -0.0101563
2 | -0.00183572 | -0.0101985 | -0.0101563
3 | -0.00189641 | -0.0101563 | -0.0101563
4 | 0 | -0.0101563 | -0.0101563
5 | 0 | -0.0101563 | -0.0101563
6 | 0 | -0.0101563 | -0.0101563
7 | 0 | -0.0101563 | -0.0101563
8 | 0.00195709 | -0.0101985 | -0.0101563
9 | 6.0685e-05 | -0.0101985 | -0.0101563
10 | 0.00201778 | -0.0102406 | -0.0101563
11 | 0.00012137 | -0.0102406 | -0.0101563
12 | 0.00207846 | -0.0102828 | -0.0101563
13 | -0.00177504 | -0.0102406 | -0.0101563
14 | 0.00207846 | -0.0102828 | -0.0101563
15 | 0.000182055 | -0.0102828 | -0.0101563
16 | 0.000182055 | -0.0102828 | -0.0101563
17 | 0.000182055 | -0.0102828 | -0.0101563
18 | 0.000182055 | -0.0102828 | -0.0101563
19 | 0.00213915 | -0.0103249 | -0.0101563
20 | -0.00171435 | -0.0102828 | -0.0101563
21 | -0.00177504 | -0.0102406 | -0.0101563
22 | 0.00012137 | -0.0102406 | -0.0101563
23 | -0.00183572 | -0.0101985 | -0.0101563
24 | 6.0685e-05 | -0.0101985 | -0.0101563
25 | 6.0685e-05 | -0.0101985 | -0.0101563
26 | -0.00189641 | -0.0101563 | -0.0101563
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

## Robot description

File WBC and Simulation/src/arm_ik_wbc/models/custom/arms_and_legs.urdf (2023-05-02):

<?xml version="1.0" encoding="utf-8"?>
<robot name="Custom_Upper_Body">


	  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
  	
  	
	<link name="base">
		<mass value="0.3"/>
		<inertial>
			<origin xyz="0 0 0" rpy="0 0 0"></origin>
			<mass value="0.3"></mass>
			<inertia ixx="0.000444379589701896" ixy="0" ixz="0" iyy="0.00048561348802354" iyz="0" izz="0.000421911604661064"></inertia>
		</inertial>
		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
	</link>
	
	<joint name="base_to_r_shoulder_yaw" type="revolute">
	    <parent link="base"/>
	    <child link="r_shoulder_yaw"/>
	    <origin xyz="0.16 0. 0.15" rpy="0 0 0"/>
	    <axis xyz="0 0 1"></axis>
	    <limit effort="3.1" lower="-1.57" upper="1.57" velocity="7.0"></limit>
  	</joint>
	
	<link name="r_shoulder_yaw">
		<inertial>
			<origin xyz="0 0 0" rpy="0 0 0"></origin>
			<mass value="0.1"></mass>
			<inertia ixx="0.000444379589701896" ixy="0" ixz="0" iyy="0.00048561348802354" iyz="0" izz="0.000421911604661064"></inertia>
		</inertial>
		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
	</link>
	
	<joint name="r_shoulder_yaw_to_shoulder_roll" type="revolute">
	    <parent link="r_shoulder_yaw"/>
	    <child link="r_shoulder_roll"/>
	    <origin xyz="0.018 0 0" rpy="0 1.57 0"/>
	    <axis xyz="0 0 1"></axis>
	    <limit effort="3.1" lower="-1.57" upper="1.57" velocity="7.0"></limit>
  	</joint>
	
	<link name="r_shoulder_roll">
		<inertial>
			<origin xyz="0 0 0" rpy="0 0 0"></origin>
			<mass value="0.1"></mass>
			<inertia ixx="0.000444379589701896" ixy="0" ixz="0" iyy="0.00048561348802354" iyz="0" izz="0.000421911604661064"></inertia>
		</inertial>
		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
	</link>
	
	<joint name="r_shoulder_roll_to_shoulder_pitch" type="revolute">
	    <parent link="r_shoulder_roll"/>
	    <child link="r_shoulder_pitch"/>
	    <origin xyz="0 0 0.018" rpy="1.57 0 0"/>
	    <axis xyz="0 0 1"></axis>
	    <limit effort="3.1" lower="-1.57" upper="1.57" velocity="7.0"></limit>
  	</joint>
	
	<link name="r_shoulder_pitch">
		<inertial>
			<origin xyz="0 0 0" rpy="0 0 0"></origin>
			<mass value="0.1"></mass>
			<inertia ixx="0.000444379589701896" ixy="0" ixz="0" iyy="0.00048561348802354" iyz="0" izz="0.000421911604661064"></inertia>
		</inertial>
		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
	</link>
	
	<joint name="r_shoulder_pitch_to_upper_arm" type="fixed">
	    <parent link="r_shoulder_pitch"/>
	    <child link="r_upper_arm"/>
	    <origin xyz="0 0.075 0" rpy="0 0 0"/>
	    <axis xyz="0 0 1"></axis>
  	</joint>
	
	<link name="r_upper_arm">
		<inertial>
			<origin xyz="0 0 0" rpy="0 0 0"></origin>
			<mass value="0.1"></mass>
			<inertia ixx="0.000444379589701896" ixy="0" ixz="0" iyy="0.00048561348802354" iyz="0" izz="0.000421911604661064"></inertia>
		</inertial>
		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
	</link>
	
	<joint name="r_upper_arm_to_elbow" type="revolute">
	    <parent link="r_upper_arm"/>
	    <child link="r_elbow"/>
	    <origin xyz="0 0.08 0" rpy="0 -1.57 0"/>
	    <axis xyz="0 0 1"></axis>
	    <limit effort="3.1" lower="-.57" upper="1.57" velocity="7.0"></limit>
  	</joint>
	
	<link name="r_elbow">
		<inertial>
			<origin xyz="0 0 0" rpy="0 0 0"></origin>
			<mass value="0.1"></mass>
			<inertia ixx="0.000444379589701896" ixy="0" ixz="0" iyy="0.00048561348802354" iyz="0" izz="0.000421911604661064"></inertia>
		</inertial>
		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
	</link>
	
	<joint name="r_elbow_to_forearm" type="fixed">
	    <parent link="r_elbow"/>
	    <child link="r_forearm"/>
	    <origin xyz="0 0.08 0" rpy="0 0 0"/>
	    <axis xyz="0 0 1"></axis>
  	</joint>
	
	<link name="r_forearm">
		<inertial>
			<origin xyz="0 0 0" rpy="0 0 0"></origin>
			<mass value="0.1"></mass>
			<inertia ixx="0.000444379589701896" ixy="0" ixz="0" iyy="0.00048561348802354" iyz="0" izz="0.000421911604661064"></inertia>
		</inertial>
		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
	</link>
	
	<joint name="r_forearm_to_wrist_1" type="revolute">
	    <parent link="r_forearm"/>
	    <child link="r_wrist_1"/>
	    <origin xyz="0 0.08 0" rpy="0 0 0"/>
	    <axis xyz="0 0 1"></axis>
	    <limit effort="3.1" lower="-1.57" upper="1.57" velocity="7.0"></limit>
  	</joint>
	
	<link name="r_wrist_1">
		<inertial>
			<origin xyz="0 0 0" rpy="0 0 0"></origin>
			<mass value="0.1"></mass>
			<inertia ixx="0.000444379589701896" ixy="0" ixz="0" iyy="0.00048561348802354" iyz="0" izz="0.000421911604661064"></inertia>
		</inertial>
		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
	</link>
	
	<joint name="r_wrist_1_to_wrist_2" type="revolute">
	    <parent link="r_wrist_1"/>
	    <child link="r_wrist_2"/>
	    <origin xyz="0 0.02 0" rpy="0 -1.57 0"/>
	    <axis xyz="0 0 1"></axis>
	    <limit effort="3.1" lower="-1.57" upper="1.57" velocity="7.0"></limit>
  	</joint>
	
	<link name="r_wrist_2">
		<inertial>
			<origin xyz="0 0 0" rpy="0 0 0"></origin>
			<mass value="0.1"></mass>
			<inertia ixx="0.000444379589701896" ixy="0" ixz="0" iyy="0.00048561348802354" iyz="0" izz="0.000421911604661064"></inertia>
		</inertial>
		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
	</link>
	
	<joint name="r_wrist_2_to_hand" type="fixed">
	    <parent link="r_wrist_2"/>
	    <child link="r_hand"/>
	    <origin xyz="0 0.04 0" rpy="0 0 0"/>
	    <axis xyz="0 0 1"></axis>
  	</joint>
	
	<link name="r_hand">
		<inertial>
			<origin xyz="0 0 0" rpy="0 0 0"></origin>
			<mass value="0.1"></mass>
			<inertia ixx="0.000444379589701896" ixy="0" ixz="0" iyy="0.00048561348802354" iyz="0" izz="0.000421911604661064"></inertia>
		</inertial>
		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
	</link>
	
	<joint name="r_end_effector" type="fixed">
	    <parent link="r_hand"/>
	    <child link="r_ee_link"/>
	    <origin xyz="0 0 0" rpy="0 0 0"/>
	    <axis xyz="0 0 1"></axis>
  	</joint>
  	
  	<link name="r_ee_link">
        <inertial>
          <mass value="0.001" />
          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
        </inertial>
      </link>
      
      
      
      
      
      
      <joint name="base_to_l_shoulder_yaw" type="revolute">
	    <parent link="base"/>
	    <child link="l_shoulder_yaw"/>
	    <origin xyz="-0.16 0. 0.15" rpy="0 0 0"/>
	    <axis xyz="0 0 -1"></axis>
	    <limit effort="3.1" lower="-1.57" upper="1.57" velocity="7.0"></limit>
  	</joint>
	
	<link name="l_shoulder_yaw">
		<inertial>
			<origin xyz="0 0 0" rpy="0 0 0"></origin>
			<mass value="0.1"></mass>
			<inertia ixx="0.000444379589701896" ixy="0" ixz="0" iyy="0.00048561348802354" iyz="0" izz="0.000421911604661064"></inertia>
		</inertial>
		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
	</link>
	
	<joint name="l_shoulder_yaw_to_shoulder_roll" type="revolute">
	    <parent link="l_shoulder_yaw"/>
	    <child link="l_shoulder_roll"/>
	    <origin xyz="-0.018 0 0" rpy="0 -1.57 0"/>
	    <axis xyz="0 0 -1"></axis>
	    <limit effort="3.1" lower="-1.57" upper="1.57" velocity="7.0"></limit>
  	</joint>
	
	<link name="l_shoulder_roll">
		<inertial>
			<origin xyz="0 0 0" rpy="0 0 0"></origin>
			<mass value="0.1"></mass>
			<inertia ixx="0.000444379589701896" ixy="0" ixz="0" iyy="0.00048561348802354" iyz="0" izz="0.000421911604661064"></inertia>
		</inertial>
		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
	</link>
	
	<joint name="l_shoulder_roll_to_shoulder_pitch" type="revolute">
	    <parent link="l_shoulder_roll"/>
	    <child link="l_shoulder_pitch"/>
	    <origin xyz="0 0 0.018" rpy="1.57 0 0"/>
	    <axis xyz="0 0 -1"></axis>
	    <limit effort="3.1" lower="-1.57" upper="1.57" velocity="7.0"></limit>
  	</joint>
	
	<link name="l_shoulder_pitch">
		<inertial>
			<origin xyz="0 0 0" rpy="0 0 0"></origin>
			<mass value="0.1"></mass>
			<inertia ixx="0.000444379589701896" ixy="0" ixz="0" iyy="0.00048561348802354" iyz="0" izz="0.000421911604661064"></inertia>
		</inertial>
		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
	</link>
	
	<joint name="l_shoulder_pitch_to_upper_arm" type="fixed">
	    <parent link="l_shoulder_pitch"/>
	    <child link="l_upper_arm"/>
	    <origin xyz="0 0.075 0" rpy="0 0 0"/>
	    <axis xyz="0 0 1"></axis>
  	</joint>
	
	<link name="l_upper_arm">
		<inertial>
			<origin xyz="0 0 0" rpy="0 0 0"></origin>
			<mass value="0.1"></mass>
			<inertia ixx="0.000444379589701896" ixy="0" ixz="0" iyy="0.00048561348802354" iyz="0" izz="0.000421911604661064"></inertia>
		</inertial>
		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
	</link>
	
	<joint name="l_upper_arm_to_elbow" type="revolute">
	    <parent link="l_upper_arm"/>
	    <child link="l_elbow"/>
	    <origin xyz="0 0.08 0" rpy="0 1.57 0"/>
	    <axis xyz="0 0 -1"></axis>
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

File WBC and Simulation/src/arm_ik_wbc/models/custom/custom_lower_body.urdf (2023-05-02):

<?xml version="1.0" encoding="utf-8"?>
<robot name="Custom_Upper_Body">


	  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
  	
  	
	<link name="base">
		<mass value="0.3"/>
		<inertial>
			<origin xyz="0 0 0" rpy="0 0 0"></origin>
			<mass value="0.3"></mass>
			<inertia ixx="0.000444379589701896" ixy="0" ixz="0" iyy="0.00048561348802354" iyz="0" izz="0.000421911604661064"></inertia>
		</inertial>
		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
	</link>
	
	<joint name="z_base_to_r_hip_yaw" type="revolute">
	    <parent link="base"/>
	    <child link="r_hip_yaw"/>
	    <origin xyz="0.1 0. -0.205" rpy="0 0 0"/>
	    <axis xyz="0 0 -1"></axis>
	    <limit effort="3.1" lower="-1.57" upper="1.57" velocity="7.0"></limit>
  	</joint>
	
	<link name="r_hip_yaw">
		<inertial>
			<origin xyz="0 0 0" rpy="0 0 0"></origin>
			<mass value="0.1"></mass>
			<inertia ixx="0.000444379589701896" ixy="0" ixz="0" iyy="0.00048561348802354" iyz="0" izz="0.000421911604661064"></inertia>
		</inertial>
		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
	</link> 
	
	<joint name="r_hip_yaw_to_pitch" type="revolute">
	    <parent link="r_hip_yaw"/>
	    <child link="r_hip_pitch"/>
	    <origin xyz="0. 0. -0.015" rpy="1.57 0 0"/>
	    <axis xyz="0 0 1"></axis>
	    <limit effort="3.1" lower="-1.57" upper="1.57" velocity="7.0"></limit>
  	</joint>
	
	<link name="r_hip_pitch">
		<inertial>
			<origin xyz="0 0 0" rpy="0 0 0"></origin>
			<mass value="0.1"></mass>
			<inertia ixx="0.000444379589701896" ixy="0" ixz="0" iyy="0.00048561348802354" iyz="0" izz="0.000421911604661064"></inertia>
		</inertial>
		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
	</link>
	
	<joint name="r_hip_pitch_to_roll" type="revolute">
	    <parent link="r_hip_pitch"/>
	    <child link="r_hip_roll"/>
	    <origin xyz="0. -0.02 0." rpy="0 1.57 0"/>
	    <axis xyz="0 0 1"></axis>
	    <limit effort="3.1" lower="-1.57" upper="1.57" velocity="7.0"></limit>
  	</joint>
	
	<link name="r_hip_roll">
		<inertial>
			<origin xyz="0 0 0" rpy="0 0 0"></origin>
			<mass value="0.1"></mass>
			<inertia ixx="0.000444379589701896" ixy="0" ixz="0" iyy="0.00048561348802354" iyz="0" izz="0.000421911604661064"></inertia>
		</inertial>
		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
	</link>
	
	<joint name="r_hip_roll_to_upper_leg" type="fixed">
	    <parent link="r_hip_roll"/>
	    <child link="r_upper_leg"/>
	    <origin xyz="0 -0.08 0" rpy="0 0 0"/>
	    <axis xyz="0 0 1"></axis>
  	</joint>
	
	<link name="r_upper_leg">
		<inertial>
			<origin xyz="0 0 0" rpy="0 0 0"></origin>
			<mass value="0.1"></mass>
			<inertia ixx="0.000444379589701896" ixy="0" ixz="0" iyy="0.00048561348802354" iyz="0" izz="0.000421911604661064"></inertia>
		</inertial>
		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
	</link>
	
	
	<joint name="r_upper_leg_to_knee" type="revolute">
	    <parent link="r_upper_leg"/>
	    <child link="r_knee"/>
	    <origin xyz="0 -0.08 0" rpy="0 0 0"/>
	    <axis xyz="0 0 -1"></axis>
	    <limit effort="3.1" lower="-.57" upper="1.57" velocity="7.0"></limit>
  	</joint>
	
	<link name="r_knee">
		<inertial>
			<origin xyz="0 0 0" rpy="0 0 0"></origin>
			<mass value="0.1"></mass>
			<inertia ixx="0.000444379589701896" ixy="0" ixz="0" iyy="0.00048561348802354" iyz="0" izz="0.000421911604661064"></inertia>
		</inertial>
		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
	</link>
	
	<joint name="r_knee_to_lower_leg" type="fixed">
	    <parent link="r_knee"/>
	    <child link="r_lower_leg"/>
	    <origin xyz="0 -0.08 0" rpy="0 0 0"/>
	    <axis xyz="0 0 1"></axis>
  	</joint>
	
	<link name="r_lower_leg">
		<inertial>
			<origin xyz="0 0 0" rpy="0 0 0"></origin>
			<mass value="0.1"></mass>
			<inertia ixx="0.000444379589701896" ixy="0" ixz="0" iyy="0.00048561348802354" iyz="0" izz="0.000421911604661064"></inertia>
		</inertial>
		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
	</link>
	
	<joint name="r_lower_leg_to_ankle" type="revolute">
	    <parent link="r_lower_leg"/>
	    <child link="r_ankle"/>
	    <origin xyz="0 -0.08 0" rpy="0 1.57 0"/>
	    <axis xyz="0 0 -1"></axis>
	    <limit effort="3.1" lower="-.57" upper="1.57" velocity="7.0"></limit>
  	</joint>
	
	<link name="r_ankle">
		<inertial>
			<origin xyz="0 0 0" rpy="0 0 0"></origin>
			<mass value="0.1"></mass>
			<inertia ixx="0.000444379589701896" ixy="0" ixz="0" iyy="0.00048561348802354" iyz="0" izz="0.000421911604661064"></inertia>
		</inertial>
		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
	</link>
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

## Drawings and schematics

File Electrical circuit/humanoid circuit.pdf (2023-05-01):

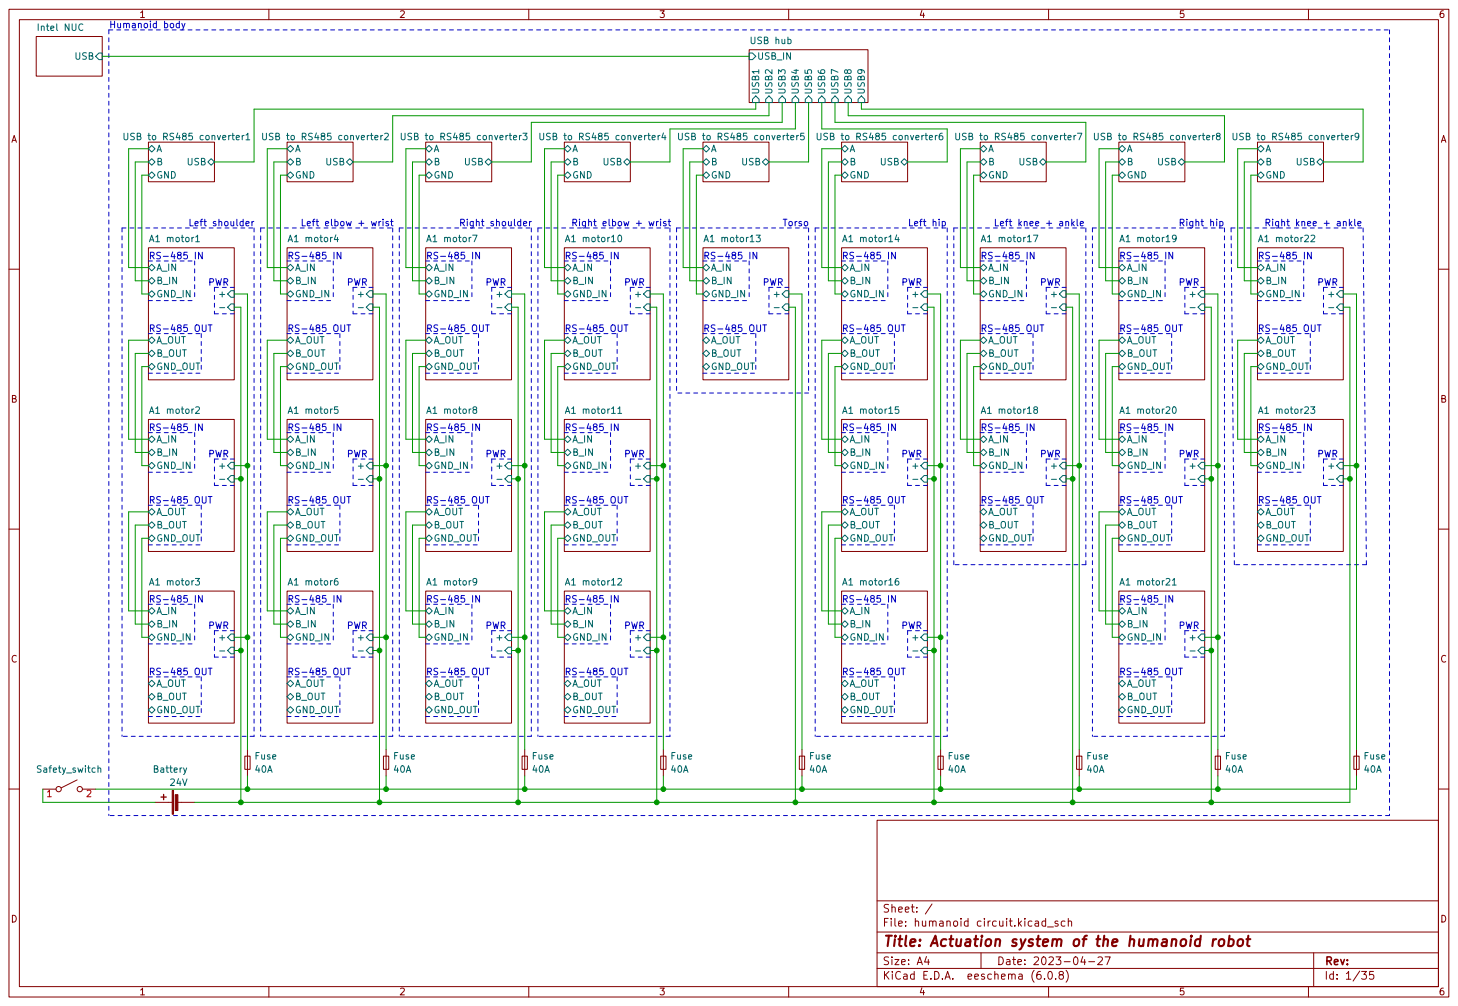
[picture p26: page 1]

RS-485 OUT Humanoid body
- A1 motor4 GND_OUT A_IN

- A1 motor7 GND_OUT A_IN
RS-485 OUT RS-485 IN

A USB to RS485 converter7 GND_OUT A_IN
RS-485 OUT Right hip RS-485 IN

Left knee + ankle PWR

- A1 motor11 GND_OUT A_IN

File: humanoid circuit.kicad_sch Sheet: / GND_OUT A_IN

Id: 1/35 Title: Actuation system of the humanoid robot

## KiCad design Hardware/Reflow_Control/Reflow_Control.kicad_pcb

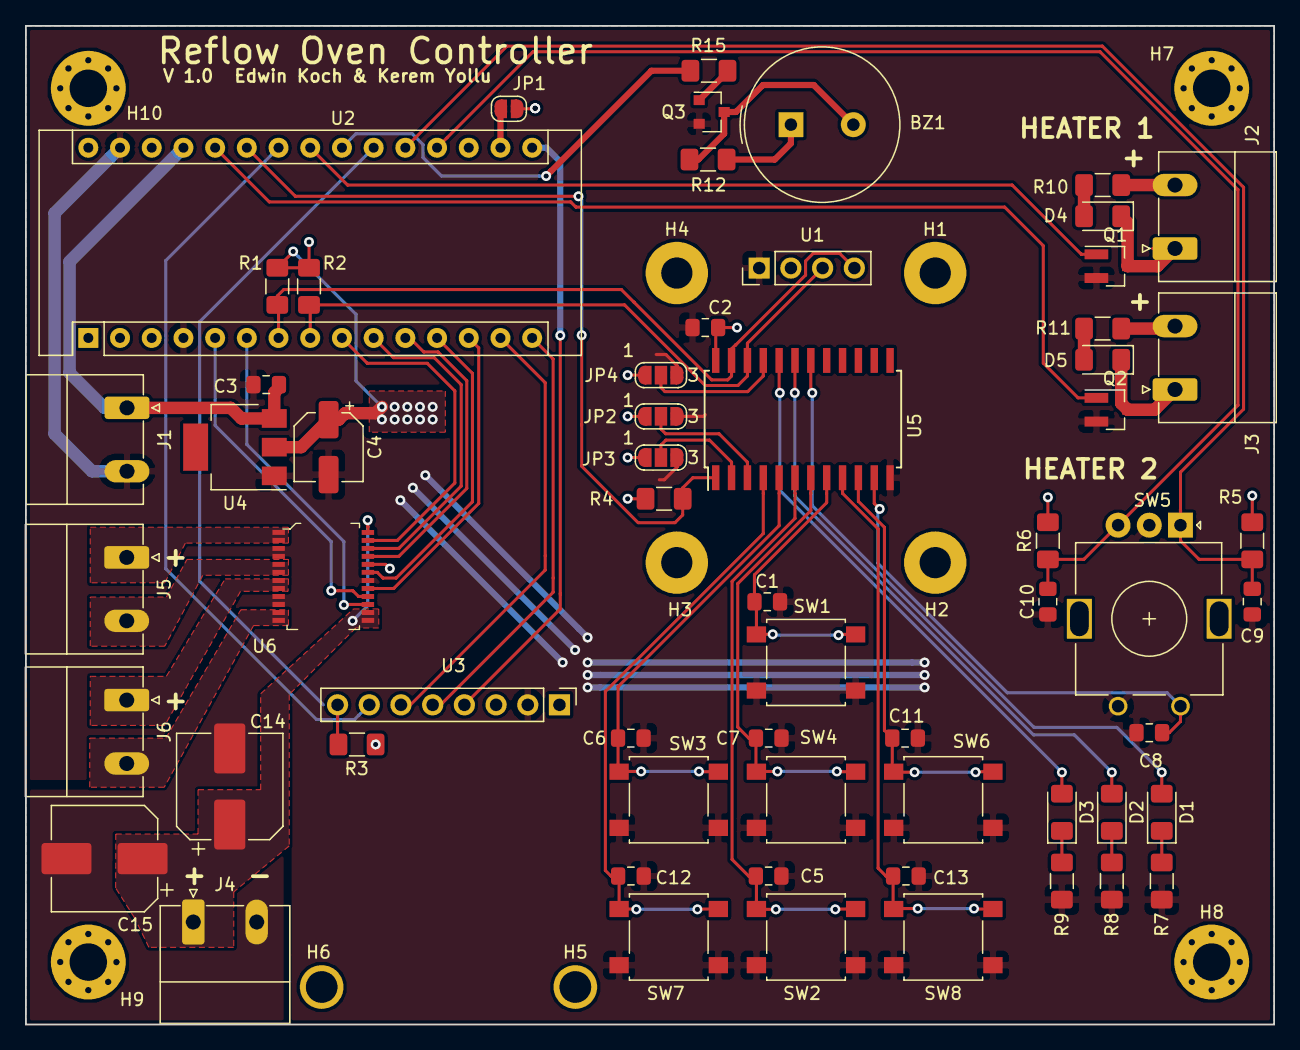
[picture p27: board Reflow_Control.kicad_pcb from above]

Board: 2 copper layers, 100.0 x 80.0 mm, 71 parts (0 on the bottom side), 52 nets.

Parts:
BZ1: Buzzer; Buzzer_TDK_PS1240P02BT_D12.2mm_H6.5mm
C1, C3, C5, C6, C7, C8, C9, C10, C11, C12, C13: 10uF; C_0805_2012Metric_Pad1.15x1.40mm_HandSolder
C2: 100n; C_0805_2012Metric_Pad1.15x1.40mm_HandSolder
C4: 100uF; CP_Elec_5x5.4
C14, C15: 100uF; CP_Elec_8x6.2
D1, D2, D3, D4, D5: LED; LED_1206_3216Metric_Pad1.42x1.75mm_HandSolder
H1, H2, H3, H4, H5, H6: MountingHole; MountingHole_2.5mm_Pad
H7, H8, H9, H10: MountingHole; MountingHole_3mm_Pad_Via
J1: Conn_5V; PhoenixContact_MC_1,5_2-G-5.08_1x02_P5.08mm_Horizontal
J2: Conn_ssr_1; PhoenixContact_MC_1,5_2-G-5.08_1x02_P5.08mm_Horizontal
J3: Conn_ssr_2; PhoenixContact_MC_1,5_2-G-5.08_1x02_P5.08mm_Horizontal
J4: Conn_mot_PWR; PhoenixContact_MC_1,5_2-G-5.08_1x02_P5.08mm_Horizontal
J5: Conn_mot_1; PhoenixContact_MC_1,5_2-G-5.08_1x02_P5.08mm_Horizontal
J6: Conn_mot_2; PhoenixContact_MC_1,5_2-G-5.08_1x02_P5.08mm_Horizontal
JP1: 3.3V Jumper; SolderJumper-2_P1.3mm_Open_RoundedPad1.0x1.5mm
JP2, JP3, JP4: ADDR_A2; SolderJumper-3_P1.3mm_Open_RoundedPad1.0x1.5mm_NumberLabels
Q1: Q_NMOS_GSD; SOT-23_Handsoldering
Q2: NUD3112LT1G; SOT-23_Handsoldering
Q3: BC848; SOT-23
R1, R2, R3, R4, R5, R6, R7, R8, R9: 4k7; R_1206_3216Metric_Pad1.42x1.75mm_HandSolder
R10, R11, R12, R15: 1k; R_1206_3216Metric_Pad1.42x1.75mm_HandSolder
SW1, SW2, SW3, SW4, SW6, SW7, SW8: SW_Push; SW_SPST_B3S-1000
SW5: Rotary_Encoder_Switch; RotaryEncoder_Alps_EC11E_Vertical_H20mm
U1: SSD1306_128x64; PinHeader_1x04_P2.54mm_Vertical
U2: NUCLEO-F042K6; Arduino_Nano
U3: MAX31865_Breakout; PinHeader_1x08_P2.54mm_Vertical
U4: LM1117-3.3; SOT-223
U5: PCA9555; SOIC-24W_7.5x15.4mm_P1.27mm
U6: TB6612FNG_C_8_EL; LSSOP-24_W5.6mm

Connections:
+3V3: BZ1.1, C2.2, C4.1, J2.2, J3.2, JP1.2, JP2.1, JP3.1, JP4.1, R1.1, R2.1, R3.1, R4.1, R5.1, R6.1, R10.1, R11.1, R12.1, U1.2, U3.3, U4.2, U5.24, U6.20
+5V: C3.1, J1.1, U2.27, U4.3
/motor_vcc: C14.1, C15.1, J4.1, U6.13, U6.14, U6.24
ADDR_A0: JP4.2, U5.21
ADDR_A1: JP3.2, U5.2
ADDR_A2: JP2.2, U5.3
BTN_A: C12.1, SW7.1, U5.4
BTN_B: C13.1, SW8.1, U5.9
BTN_CENTER: C7.1, SW4.1, U5.7
BTN_DOWN: C5.1, SW2.1, U5.6
BTN_LEFT: C6.1, SW3.1, U5.5
BTN_RIGHT: C11.1, SW6.1, U5.10
BTN_UP: C1.1, SW1.1, U5.8
CH1_MOTOR_IN1: U2.11, U6.21
CH1_MOTOR_IN2: U2.10, U6.22
CH1_MOTOR_STBY: U2.12, U6.19
CH2_MOTOR_IN1: U2.5, U6.16
CH2_MOTOR_IN2: U2.13, U6.17
ENC_Switch: C8.2, SW5.S1, U5.11
GND: C1.2, C2.1, C3.2, C4.2, C5.2, C6.2, C7.2, C8.1, C9.1, C10.1, C11.2, C12.2, C13.2, C14.2, C15.2, J1.2, J4.2, JP2.3, JP3.3, JP4.3, Q1.2, Q2.2, Q3.2, R7.2, R8.2, R9.2, SW1.2, SW2.2, SW3.2, SW4.2, SW5.C, SW5.S2, SW6.2, SW7.2, SW8.2, U1.1, U2.4, U2.29, U3.2, U4.1, U5.12, U6.3, U6.4, U6.9, U6.10, U6.18
I2C1_SCL: R2.2, U1.3, U2.8, U5.22
I2C1_SDA: R1.2, U1.4, U2.7, U5.23
INT_ENC_A: C10.2, R6.2, SW5.B, U2.19
INT_ENC_B: C9.2, R5.2, SW5.A, U2.20
INT_MAX31865_RDY: R3.2, U2.21, U3.8
INT_PCA9555: R4.2, U2.25, U5.1
unnamed: BZ1.2, Q3.3, R12.2
unnamed: D1.1, R7.1
unnamed: D1.2, U5.18
unnamed: D2.1, R8.1
unnamed: D2.2, U5.19
unnamed: D3.1, R9.1
unnamed: D3.2, U5.20
unnamed: D4.1, J2.1, Q1.3
unnamed: D4.2, R10.2
unnamed: D5.1, J3.1, Q2.3
unnamed: D5.2, R11.2
unnamed: J5.1, U6.1, U6.2
unnamed: J5.2, U6.5, U6.6
unnamed: J6.1, U6.7, U6.8
unnamed: J6.2, U6.11, U6.12
unnamed: JP1.1, U2.17
unnamed: Q3.1, R15.1
SPI1_CS_MAX31865: U2.24, U3.7
SPI1_MISO: U2.15, U3.5
SPI1_MOSI: U2.14, U3.6
SPI1_SCK: U2.16, U3.4
SSR_1: Q1.1, U2.23
SSR_2: Q2.1, U2.26
TIM1_CH1_PWM_Buzzer: R15.2, U2.22
TIM3_CH1_MOTOR_PWM: U2.9, U6.23
TIM3_CH2_MOTOR_PWM: U2.6, U6.15

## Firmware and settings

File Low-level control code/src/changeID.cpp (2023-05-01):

#include <stdio.h>
#include <string.h>
#include <unistd.h>
#include <stdlib.h>
#include "serialPort/SerialPort.h"

#define BroadAllMotorID     0xBB
#define MotorPulsator       11

int main(){
    char serial_name[100];

    MOTOR_send motor_s;
    MOTOR_recv motor_r;

    motor_s.motorType = MotorType::A1Go1;    // set the motor type, A1Go1 or B1
    motor_r.motorType = motor_s.motorType;

    printf("Please input the name of serial port.(e.g. Linux:/dev/ttyUSB0, Windows:\\\\.\\COM3)\n");
    scanf("%s",serial_name);
    printf("The serial port is %s\n", serial_name);

    memset(static_cast<void*>(&motor_s), 0, sizeof(motor_s));
    motor_s.id = BroadAllMotorID;
    motor_s.mode = 10;
    modify_data(&motor_s);
    printf("The motor ID is: %X\n", motor_s.motor_send_data.head.motorID);

    //进入伺服模式
    SerialPort serial(serial_name);  // set the serial port name
    serial.send((uint8_t*)&(motor_s.motor_send_data), motor_s.hex_len);

    usleep(100000);  //sleep 0.1s

    //Enter the trackwheel mode (modify ID)
    motor_s.mode = MotorPulsator;
    modify_data(&motor_s);
    serial.send((uint8_t*)&(motor_s.motor_send_data), motor_s.hex_len);

    printf("Please turn the motor.\n");
    printf("One time: id=0; Two times: id=1, Three times: id=2\n");
    printf("ID can only be 0, 1, 2\n");
    printf("Once finished, press 'a'\n");

    // int c;
    while(getchar() != (int)'a');
    printf("Turn finished\n");

    //保存ID
    motor_s.mode = 0;
    modify_data(&motor_s);
    serial.send((uint8_t*)&(motor_s.motor_send_data), motor_s.hex_len);

    MOTOR_send motor_stop;
    MOTOR_recv motor_recv;
    
    motor_stop.motorType = MotorType::A1Go1;; //set the same type of the motor for run and stop commands
    motor_stop.mode = 0;                        //set the mode of the stop command to idle
    modify_data(&motor_stop);
    for(int i = 0; i < 3; i++){
        motor_stop.id = i;               //set the same ID for run and stop commands
        serial.sendRecv(&motor_stop, &motor_recv); 
        extract_data(&motor_recv);
        if(motor_stop.id==motor_recv.motor_id){
            printf("The ID is set to %i\n", motor_recv.motor_id);
        }
    }

    return 0;
}

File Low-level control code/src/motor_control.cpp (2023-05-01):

#include <csignal>
#include <iostream>
#include <fstream>
#include <string>
#include <list> 
#include <chrono>
#include "serialPort/SerialPort.h"
#include "Motor/Motor.h"
#include "Motor/PIDcontroller.h"
#include "MotorGroup/MotorGroup.h"
#include "ActuationSystem/ActuationSystem.h"
#include "CSVGenerator/CSVGenerator.h"

#define update_frequency 1000.0f // frequency of sending commands [Hz]

//function to get inputs from terminal and return them in a list format
std::list<float> get_desired_positions_list(int number_of_motors) {
  
  std::string obtained_string;            //string to store raw input from terminal
  float new_desired_position = 0;         //variable to store converted value from terminal
  std::list<float> new_desired_positions; //list to store desired positions
  
  //for loop to get an input from terminal for every motor
  for(int i = 0; i < number_of_motors; i++) {
    std::cout << "\nEnter desired position: ";
    std::getline(std::cin, obtained_string);
    new_desired_position = std::stof(obtained_string);  // convert to float
    new_desired_positions.push_back(new_desired_position);
  }
  return new_desired_positions;
};

//simple function to stop the code
bool ask_whether_continue() {
  std::string obtained_string;
  std::cout << "\nWant to continue? y or n?";
  std::getline(std::cin, obtained_string);
  if(obtained_string == "y"){
    return true;
  }else{
    return false;
  }
};

int main(){

  //variables needed for the main function
  bool execution_flag = false;             //flag for if block terminating the code
  int i = 0;                               //iterator for the inner do while loop
  std::list<float> desired_positions_list; //list to store input from the terminal
  std::list<float> actual_positions;       //list to store positions read from the motors
  int number_of_motors = 0;

  //CSVGenerator csvgenerator;

  //constructor with execution time measurement 
  auto start = std::chrono::high_resolution_clock::now();
  ActuationSystem actuationSystem;
  auto end = std::chrono::high_resolution_clock::now();
  auto duration = std::chrono::duration_cast<std::chrono::microseconds>(end - start);
  std::cout << "Execution time of ActuationSystem constructor: " << duration.count() << " microseconds" << std::endl;
  
  //option to stop execution in this moment
  if (!(ask_whether_continue())){
    actuationSystem.stop_motors();
    std::cout << "end of run" << std::endl;
    return 0;
  } 
  
  //the main loop to run the motor and update desired positions 
  do {
    std::cout << "Entered the first loop"<< std::endl;
    std::cout << "******************" << std::endl;

    //option to stop execution in this moment
    if (!(ask_whether_continue())){
      actuationSystem.stop_motors();
      std::cout << "end of run" << std::endl;
      return 0;
    } 
    
    auto start2 = std::chrono::high_resolution_clock::now();
    //inner loop for updating output torque, running for a fixed number of iterations 
    do{
      //std::cout << "Entered the second loop"<< std::endl;
      //std::cout << "******************" << std::endl;
      
      //try-catch block for upadting output torque
      try{

        //output torque update function with execution time measurement 
        //start = std::chrono::high_resolution_clock::now();
        actuationSystem.update_torque(); //update torque output for all connected motors
        //end = std::chrono::high_resolution_clock::now();
        //duration = std::chrono::duration_cast<std::chrono::microseconds>(end - start);
        //std::cout << "Execution time of update_torque(): " << duration.count() << " microseconds. Max f: " << (1.0f/float(duration.count()))*1000000 << std::endl;

        //csvgenerator.append_data(i, actuationSystem.read_torque(), actuationSystem.read_actual_positions(), actuationSystem.read_desired_position());

      } catch (const IOException& e) {
        std::cerr << "Error opening serial port: " << e.what() << std::endl;
      }
      i++;                       // increase iterator
      sleep(1/update_frequency); // sleep for a set period
    }while(i<2000);
    auto end2 = std::chrono::high_resolution_clock::now();
    auto duration2 = std::chrono::duration_cast<std::chrono::milliseconds>(end2 - start2);
    std::cout << "Execution time of 2000 iterations:: " << duration2.count() << " milliseconds." << std::endl;
    i=0; // reset the iterator for the next entry into the inner loop
    

    
    //read actual positions of connected motors with execution time measurement
    start = std::chrono::high_resolution_clock::now();
    actual_positions = actuationSystem.read_actual_positions(); //read actual positions of connected motors
    end = std::chrono::high_resolution_clock::now();
    duration = std::chrono::duration_cast<std::chrono::microseconds>(end - start);
    std::cout << "Execution time of read_actual_positions(): " << duration.count() << " microseconds. Max f: " << (1.0f/float(duration.count()))*1000000 << std::endl;
    
    number_of_motors = int(actual_positions.size());

    //print read positions to terminal
    std::cout << "actual_positions: ";
    for (const auto& element : actual_positions) {
        std::cout << element*(180/3.14159265359) << " ";
    }
    std::cout << std::endl;

    execution_flag = ask_whether_continue(); //option to terminate execution of the code
    
    //update desired positions of all connected motors if execution_flag is true
    if(execution_flag == true){
      std::list<float> desired_positions = get_desired_positions_list(number_of_motors); //get new desired positions from terminal in a list format

      for (auto it = desired_positions.begin(); it != desired_positions.end(); ++it) {
          *it = *it*(3.14159265359/180);
      }

      std::cout << "converted desired_positions: ";
      for (const auto& element : desired_positions) {
          std::cout << element << " ";
      }
      std::cout << std::endl;
      
      //send the new desired positions to all connected motors with execution time measurement
      start = std::chrono::high_resolution_clock::now();
      actuationSystem.send_desired_positions(desired_positions); //update desired positions of all connected motors
      end = std::chrono::high_resolution_clock::now();
      duration = std::chrono::duration_cast<std::chrono::microseconds>(end - start);
      std::cout << "Execution time of send_desired_positions(): " << duration.count() << " microseconds. Max f: " << (1.0f/float(duration.count()))*1000000 << std::endl;
    }

  }while(execution_flag);

  actuationSystem.stop_motors(); //set motors to idle mode
  //csvgenerator.safe_data();
  std::cout << "end of run" << std::endl;
  return 0;
}

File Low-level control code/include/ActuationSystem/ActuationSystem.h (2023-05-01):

#ifndef ACTUATIONSYSTEM_H
#define ACTUATIONSYSTEM_H

//maximum number of converters needed for the entire robot 
//corresponds to total number of rows (both commented out and not) in joint names in configuration.yml
#define length_of_MotorGroup_array 9 

#include <iostream>
#include <string>
#include <vector>
#include <thread>
#include "yaml-cpp/yaml.h"
#include "unitreeMotor/unitreeMotor.h"
#include "MotorGroup/MotorGroup.h"

//class for the entire actuation system of a humanoid
class ActuationSystem {
  public:
    
    //constructor
    ActuationSystem();

    //destructor
    ~ActuationSystem(); //an explicit destructor is needed to free up memory occupied by _motor_groups array

    //public member methods
    void  send_desired_positions(std::list<float> desired_positions); //function sending a list of desired positions to all connected motors
    std::list<float> read_actual_positions();                         //function returning a list of actual positions of all connected motors 
    void  update_torque();                                            //function to loop through all MotorGroup objects to calculate new value of torque
    void  update_desired_position_from_terminal();                    //function to loop through all MotorGroup objects to update the desired position from terminal (used for testing)
    void  stop_motors();                                              //function to loop through all MotorGroup objects to send a stop message, i.e., mode=0, so that all motors go to idel state
    std::vector<float> read_torque();
    std::vector<float> read_desired_position();

  private:

    //private member methods
    void read_configuration_file(); //function to extract configuratoin data from configuration.yml file

    //private member variables 
    
    //data extracted from configuration.yml file
    float _torque_limit;          //maximum magnitude of torque that can be send to a motor
    float _temp_limit;            //temperature threshold of a motor, once exceeded the motors should shutdown 
    float _refresh_frequency;     //frequency at which arrays of new desired positions will be sent
    int   _number_of_converters;  //number of connected USB-RS485 converters
    YAML::Node _joint_names_node; //names related to positions of all connected motors
    YAML::Node _PID_gains_node;   //values of P, I and D gains for every connected motor 

    
    MotorGroup* _motor_groups[length_of_MotorGroup_array]; //fixed length array of pointers to MotorGroup objects
};

ActuationSystem::ActuationSystem() {

    std::cout << "ActuationSystem.h - constructor" << std::endl; //display a message that the function was entered
    
    read_configuration_file(); //get data from the configuration file
    
    //a loop to instantiate specified number of MotorGroup objects
    for(int i = 0; i < _number_of_converters; i++){
      //try-catch block to display error message in case of unsuccessful instantiation of a MotorGroup object
      try{
        std::string port_name = "/dev/ttyUSB" + std::to_string(i); //create a name for a SerialPort object controlling a converter
        
        //a loop to populate IDs list with as many subsequent ID numbers as there is motors in a given MotorGroup object, 
        //i.e., names in a row of _joint_names_node
        std::list<int> IDs;                                        //create an empty list of motor IDs
        for (int j = 0; j < int(_joint_names_node[i].size()); j++){
          IDs.push_back(j); //add subsequent ID to the list
        }
        //IDs.push_back(i+1);

        //create a pointer to an instantiated MotorGroup object 
        //IMPORTANT: "new" keyword makes sure that the memory occupied by the pointer will not be freed up at any point of the code 
        //until explicit calling of the destructor. Without this keyword the code does not work.
        MotorGroup* _motor_group = new MotorGroup(_torque_limit, _temp_limit, _refresh_frequency, port_name, IDs, _PID_gains_node[i]);

        _motor_groups[i] = _motor_group; //add the pointer to instantiated MotorGroup object to the array with other objects of this class
        std::cout << "_motor_groups[" << i << "] assigned a pointer:" << _motor_groups[i] << std::endl; //display value of the MotorGroup object pointer
      } catch (const IOException& e) {
        std::cerr << "Error opening serial port: " << e.what() << std::endl;  //display error message in case of unsuccessful reading of the file
      }
    }
    std::cout << "ActuationSystem.h - constructor END" << std::endl; //display a message that the function ends here
    std::cout << "********************************" << std::endl;    //display a breaker at the end for better readability
}

ActuationSystem::~ActuationSystem(){
  for(int i = 0; i < _number_of_converters; i++){
    delete _motor_groups[i]; // Free memory allocated for array of MyObject
  }
}
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

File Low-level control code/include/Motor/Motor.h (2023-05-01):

#ifndef MOTOR_H
#define MOTOR_H

#define Mode 10 //operation mode of motors, 0=stall, 5=slow motion, 10=torque mode

#include <iostream>
#include <string>
#include <list>
#include "yaml-cpp/yaml.h"
#include "PIDcontroller.h"
#include "unitreeMotor/unitreeMotor.h"

//class for an A1 motor
class Motor : public PIDcontroller {
  public:
    
    //constructors
    Motor();
    Motor(float torque_limit, float temp_limit, float refresh_frequency, int line_id, int ID, YAML::Node PID_gains);

    //public member methods
    void print_init_values();                           //function to print initial values of motor's variables
    void new_torque();                                  //calculate new torque required for the motor
    void desired_position_update();                     //get new desired position from terminal (testing purposes)
    void send_desired_position(float desired_position); //set the desired position of the motor
    float read_actual_position();                       //get the actual position of the motor
    float read_desired_position();
    float read_torque();

    //public member variables 
    MOTOR_send motor_run, motor_stop; //motor send message structs for run and stop instructions
    MOTOR_recv motor_r;               //motor receive message struct for obtainig data from the motor

  private:
    
    //private member variables
    int _line_id = 0;                        //default value for line id, will be changed in the constructor
    MotorType _motorType = MotorType::A1Go1; //type of the connected motor (in this case always A1)
    float _T = 0.0;                          //forward fetched torque [Nm]
    float _W = 0.0;                          //desired angular velocity
    float _Pos = 0.0;                        //desired position
    float _K_P = 0.0;                        //gain of position error
    float _K_W = 0.0;                        //gain of velocity error
    float _gear_ratio = 9.1;                 //internal gear ratio of the motor
    float _temp_limit;
};

//default contructor
Motor::Motor() : PIDcontroller{}{

}

Motor::Motor(float torque_limit, float temp_limit, float refresh_frequency, int line_id, int ID, YAML::Node PID_gains) : PIDcontroller{torque_limit, refresh_frequency, PID_gains} {
    std::cout << "Motor.h - constructor()" << std::endl;
    _line_id = line_id;
    _temp_limit = temp_limit;
    // set the id of motor
    motor_run.motorType = _motorType; //set the motor type in the message struct
    motor_run.id = ID;                //set message ID to be matching with motor's one
    motor_run.mode = Mode;            //0: idle, 5: open loop rotation, 10: closed loop FOC control
    motor_run.T = _T;                 //forward fetched torque [Nm]
    motor_run.W = _W;                 //desired angular velocity
    motor_run.Pos = _Pos;             //desired position
    motor_run.K_P = _K_P;             //gain of position error
    motor_run.K_W = _K_W;             //gain of velocity error

    motor_stop.motorType = _motorType; //set the motor type in the message struct
    motor_stop.id = ID;                //set message ID to be matching with motor's one
    motor_stop.mode = 0;               //0: idle, 5: open loop rotation, 10: closed loop FOC control
    motor_stop.T = _T;                 //forward fetched torque [Nm]
    motor_stop.W = _W;                 //desired angular velocity
    motor_stop.Pos = _Pos;             //desired position
    motor_stop.K_P = _K_P;             //gain of position error
    motor_stop.K_W = _K_W;             //gain of velocity error

    motor_r.motorType = _motorType;    //set the motor type in the message struct

    print_init_values();               //print values of initialised motor

    //encode the data so that it can be sent
    modify_data(&motor_run);
    modify_data(&motor_stop);
}

//function to print initial values of motor's variables
void Motor::print_init_values(){
    std::cout << "Motor.h - print_init_values()" << std::endl;
    std::cout << "line: " << _line_id << std::endl;
    std::cout << "ID: " << motor_run.id << std::endl;
    std::cout << "Mode: " << motor_run.mode << std::endl;
    std::cout << "T: " << motor_run.T << std::endl;
    std::cout << "W: " << motor_run.W << std::endl;
    std::cout << "Pos: " << motor_run.Pos/_gear_ratio << std::endl;
    std::cout << "Kp: " << motor_run.K_P << std::endl;
    std::cout << "Kw: " << motor_run.K_W << std::endl;
    std::cout << "******************" << std::endl;
}

//calculate new torque required for the motor
void Motor::new_torque(){
  if(motor_r.Temp > _temp_limit){
    std::cout << "ID: " << motor_run.id << std::endl;
    std::cout << "Motor is overheating" << std::endl;
    motor_run.T = 0.0;
  } else {
    //std::cout << "ID: " << motor_run.id << std::endl;
    motor_run.T = nextValue(motor_r.Pos);
  }
}

//get new desired position from terminal (testing purposes)
void Motor::desired_position_update() {
  std::string obtained_string;
  float new_desired_position = 0;
  std::cout << "\nEnter desired position: ";
  std::getline(std::cin, obtained_string);
  new_desired_position = std::stof(obtained_string);  // convert to float
  if(get_targetPosition() != new_desired_position){
      set_targetPosition(new_desired_position);
  }
}

//set the desired position of the motor
void Motor::send_desired_position(float desired_position){
  set_targetPosition(desired_position);
}

//function to access actual position of the motor
float Motor::read_actual_position(){
  return motor_r.Pos/_gear_ratio; //divide encoder's position by gear ratio to obtain actual position of a rotor
}

float Motor::read_torque(){
  return get_PIDoutput();
}

float Motor::read_desired_position(){
  return get_desired_pos();
}
#endif

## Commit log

2023-04-30 Added robot arm CAD files (deliverable)
    [1.5x6mm Pin.SLDPRT, 12mm Bearing.SLDPRT, 12mm M4 Bracket.SLDPRT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]
2023-04-30 Changed file structure
    [1.5x6mm Pin.SLDPRT, 12mm Bearing.SLDPRT, 12mm M4 Bracket.SLDPRT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]
2023-05-01 Added electric team stuff
    Added motor test results, electrical circuit design and low-level control software
    [A1 motor.kicad_sch, KP=0.01_KI=0.01_KD=0.01_f[Hz]=500_T_limit[Nm]=0.5_Initial_error[rad]=0_bar_only.csv, KP=0.1_KI=0.01_KD=0.01_f[Hz]=500_T_limit[Nm]=0.5_Initi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]
2023-05-01 Add Encoder test results and a report from testing
    [encoder test.xlsx]
2023-05-02 will adding WBC code and simulation urdf, yaml, model files
    [A1.urdf, Aliengo.urdf, AliengoVx300.urdf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]
2023-05-03 Humanoid Robot Leg Design
    [Humanoid_Robot_Leg_Design_Final - Ankle Belt.stl, Humanoid_Robot_Leg_Design_Final - Ankle Joint Pulley.stl, Humanoid_Robot_Leg_Design_Final - Ankle Motor Pulle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]
